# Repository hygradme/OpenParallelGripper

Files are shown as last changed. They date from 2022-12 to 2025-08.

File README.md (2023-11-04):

# Electric Parallel Gripper for UFACTORY LITE 6

## Introduction
This project provides electric parallel gripper for UFACTORY LITE 6.
This gripper can also be used for UFACTORY xArm series and possibly with other industrial cobots like Universal Robot etc.

Video (pick and place example with UFACTORY LITE 6 and OPEN Parallel Gripper): https://www.youtube.com/shorts/wrYzYbHsh44

There are two version available. SCS3045M_version which is original version I made and XL330_version which I redesigned to make the gripper lighter, thinner and cheaper at the expense of rigidity.
## SCS3045M_version
Detail: [SCS3045M_version](./SCS3045M_version/README.md)

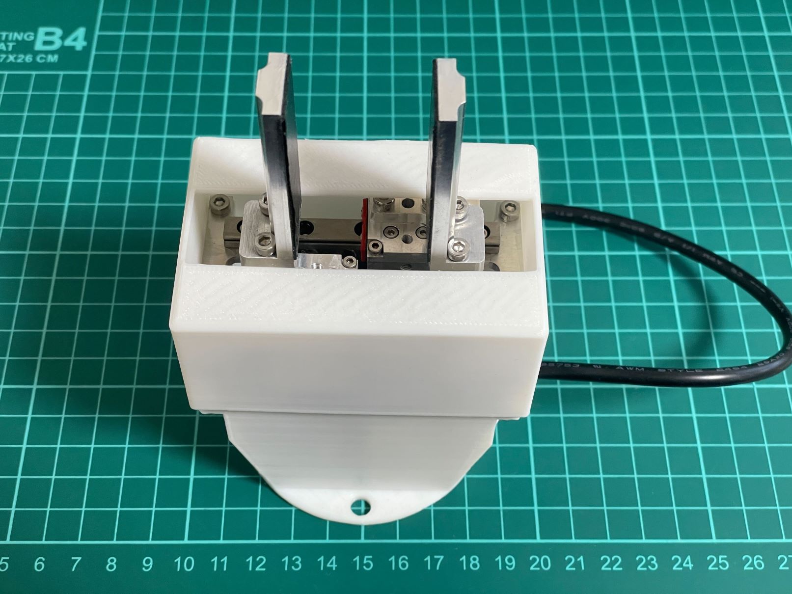
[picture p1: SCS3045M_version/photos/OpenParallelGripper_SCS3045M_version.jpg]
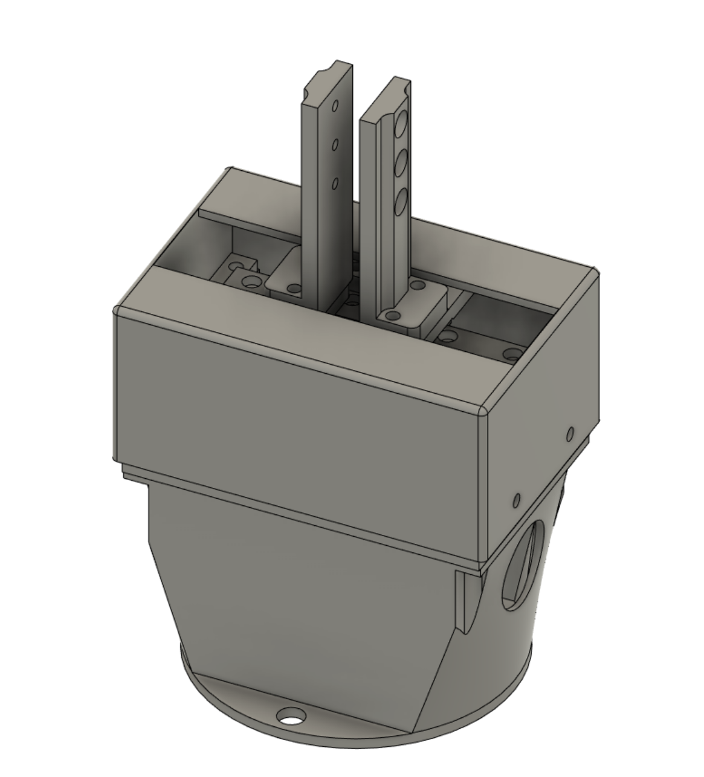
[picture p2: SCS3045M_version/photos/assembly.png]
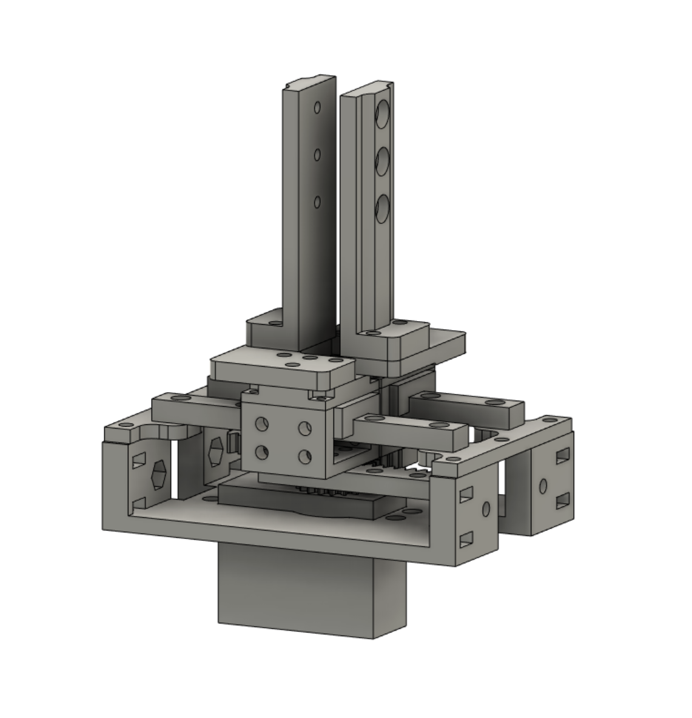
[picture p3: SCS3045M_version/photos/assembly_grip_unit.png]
  
- Use Feetech SCS3045M servo
- stroke: 0-55mm
- weight: about 340g
- Communication protocol: Two digital inputs(compatible with default LITE 6 gripper) or Modbus-RTU with RS485.

## XL330_version
Detail: [XL330_version](./XL330_version/README.md)

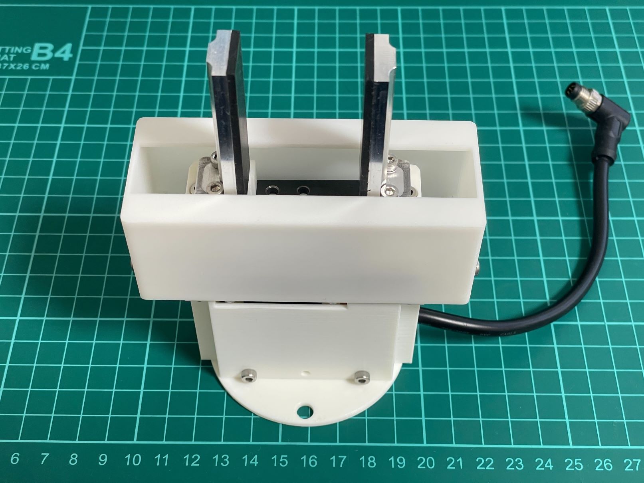
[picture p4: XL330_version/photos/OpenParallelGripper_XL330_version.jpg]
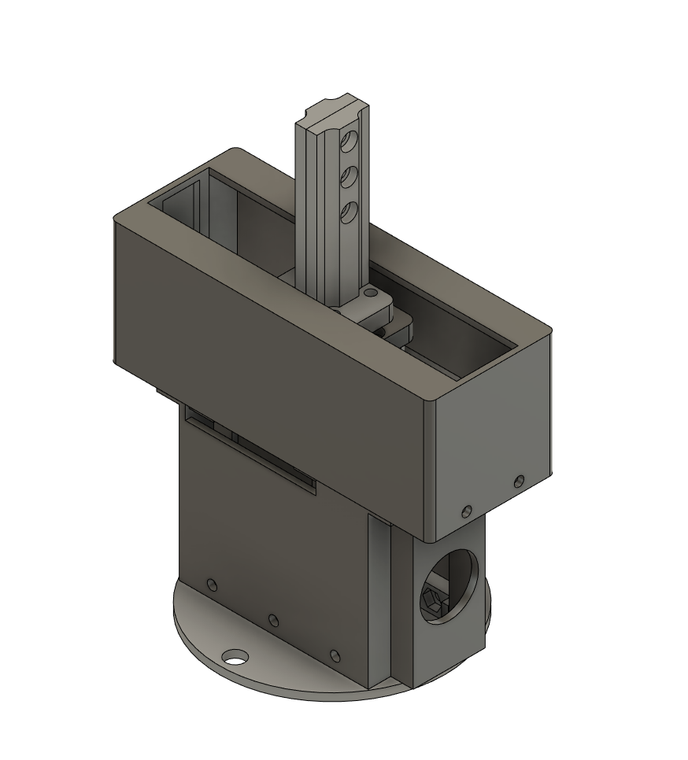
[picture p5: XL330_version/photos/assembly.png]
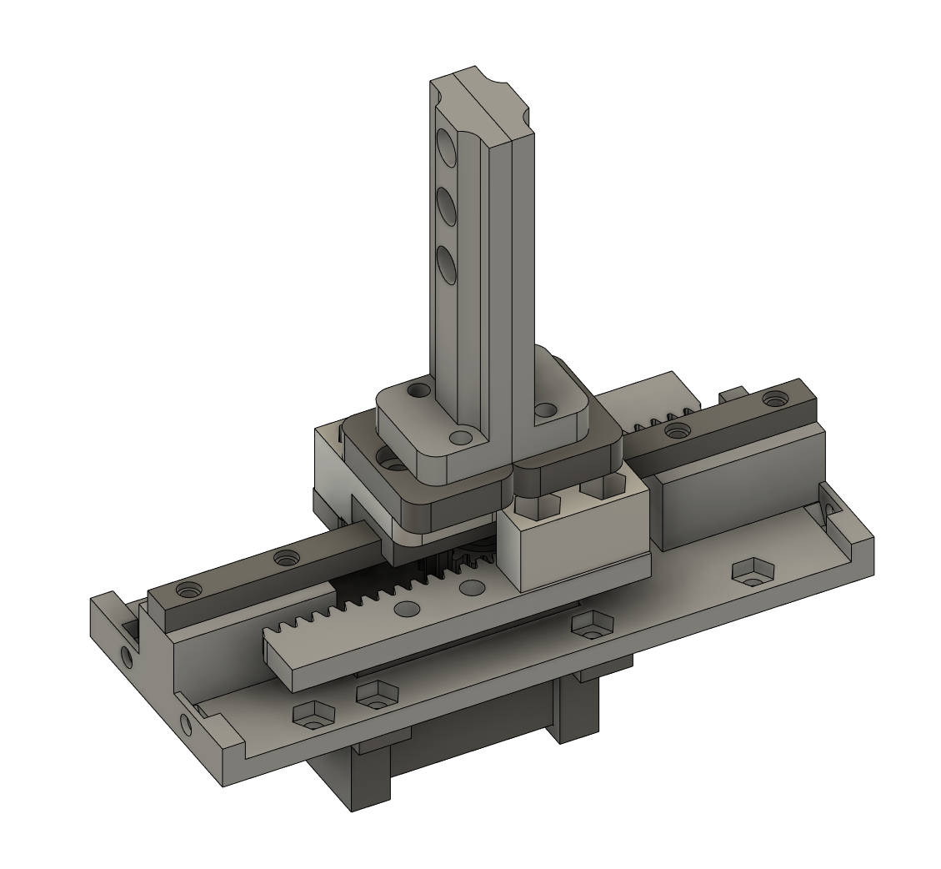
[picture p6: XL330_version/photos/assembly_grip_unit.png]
  
- Use Dynamixel XL330-M288-T servo
- stroke: 0-65mm
- weight: about 270g
- Communication protocol: Two digital inputs(compatible with default LITE 6 gripper) or Modbus-RTU with RS485.

## Contact
https://twitter.com/EL2031watson

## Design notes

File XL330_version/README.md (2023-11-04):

# Electric Parallel Gripper for UFACTORY LITE 6(XL330 version)

## Introduction
This project provides electric parallel gripper for UFACTORY LITE 6.
This gripper can also be used for UFACTORY xArm series and possibly with other industrial cobots like Universal Robot etc.

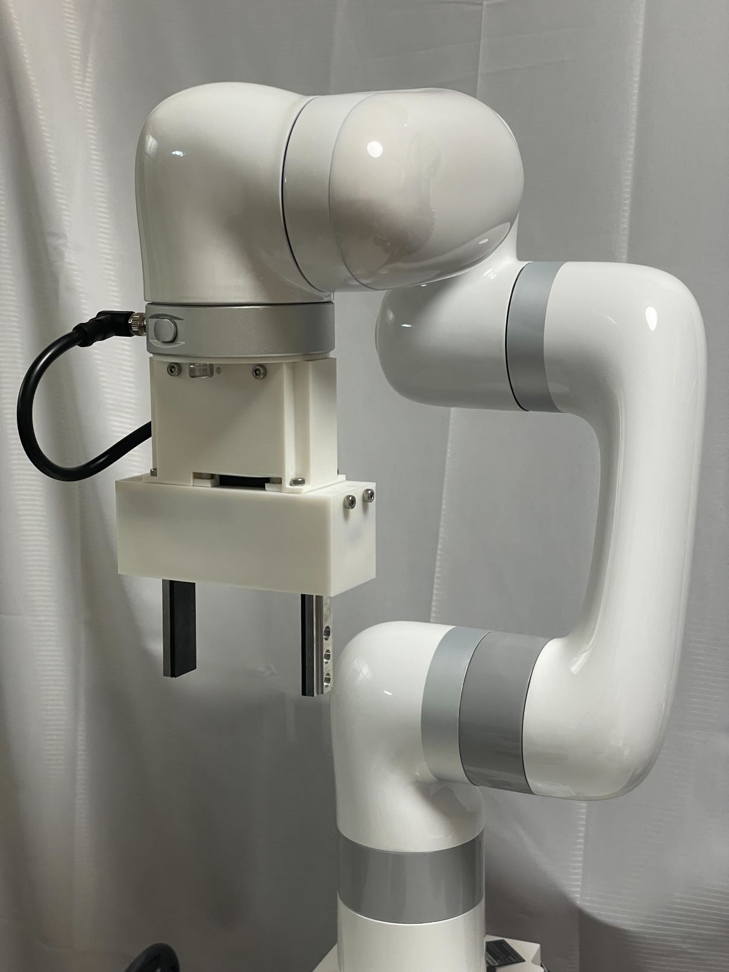
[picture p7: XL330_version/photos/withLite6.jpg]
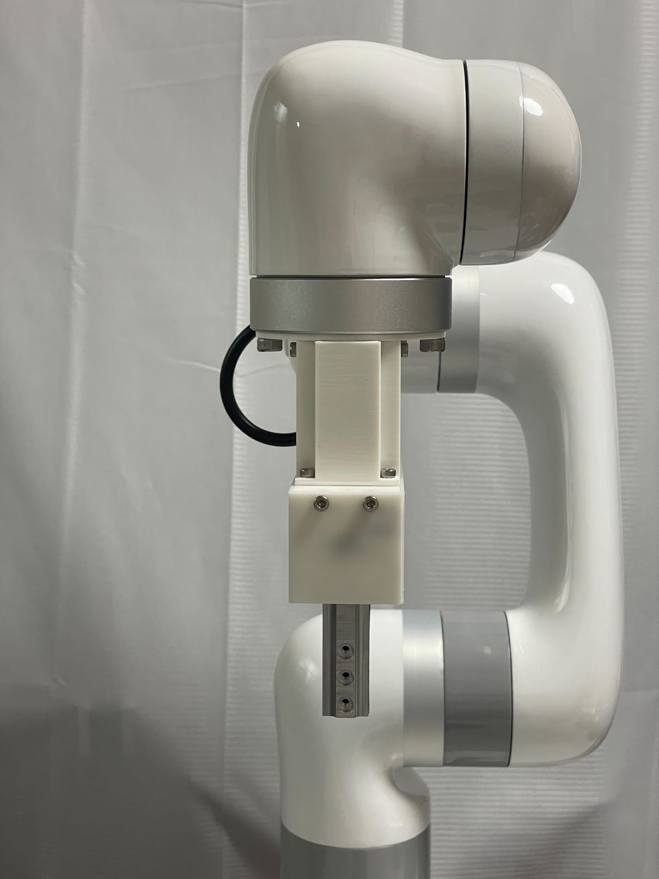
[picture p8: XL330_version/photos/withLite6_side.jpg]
 



 

Video (pick and place example with UFACTORY LITE 6 and OPEN Parallel Gripper): https://youtube.com/shorts/0Ie3bUuqNkI?si=m0Drl9e4QJItGcFO

## Spec of the gripper
- stroke: 0-65mm
- weight: about 270g
- Communication protocol: Two digital inputs(compatible with default LITE 6 gripper) or Modbus-RTU with RS485.

## BOM
Check [BOM](./hardware/BOM.md)

## Assemble instruction
Not yet avaialble.

## Electronics
See [Electronics](./electronics/README.md)
## Software
See [Software](./software/README.md)

If you prefer to use two digital inputs to control the gripper for simplicity, you can use xArm SDK from UFACTORY(https://github.com/xArm-Developer/xArm-Python-SDK/blob/master/xarm/wrapper/xarm_api.py#L3654).

If you want to control the gripper more detail, you need to use Modbus-RTU with RS485.

## Contact
https://twitter.com/EL2031watson

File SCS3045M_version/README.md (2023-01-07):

# Electric Parallel Gripper for UFACTORY LITE 6

## Introduction
This project provides electric parallel gripper for UFACTORY LITE 6.
This gripper can also be used for UFACTORY xArm series and possibly with other industrial cobots like Universal Robot etc.

 
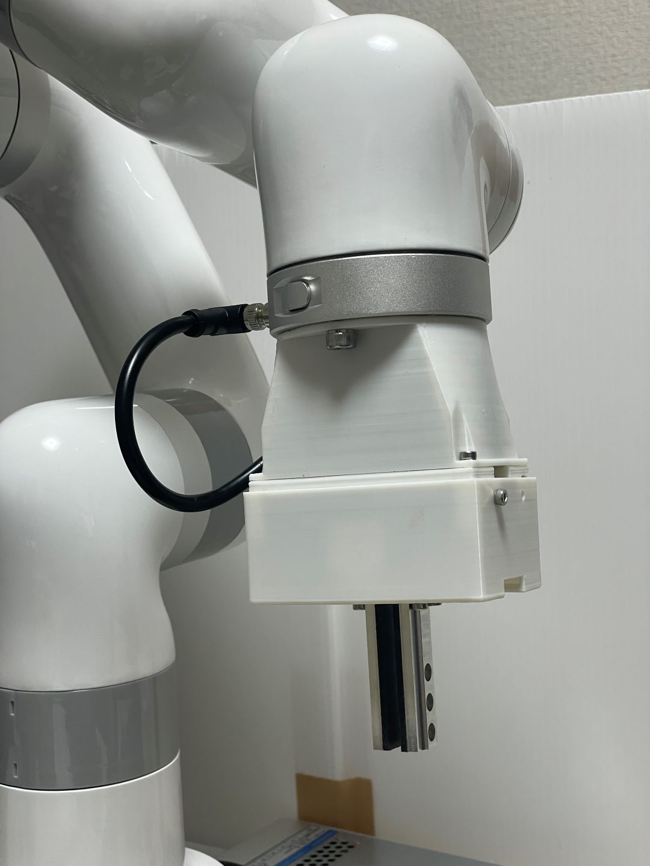
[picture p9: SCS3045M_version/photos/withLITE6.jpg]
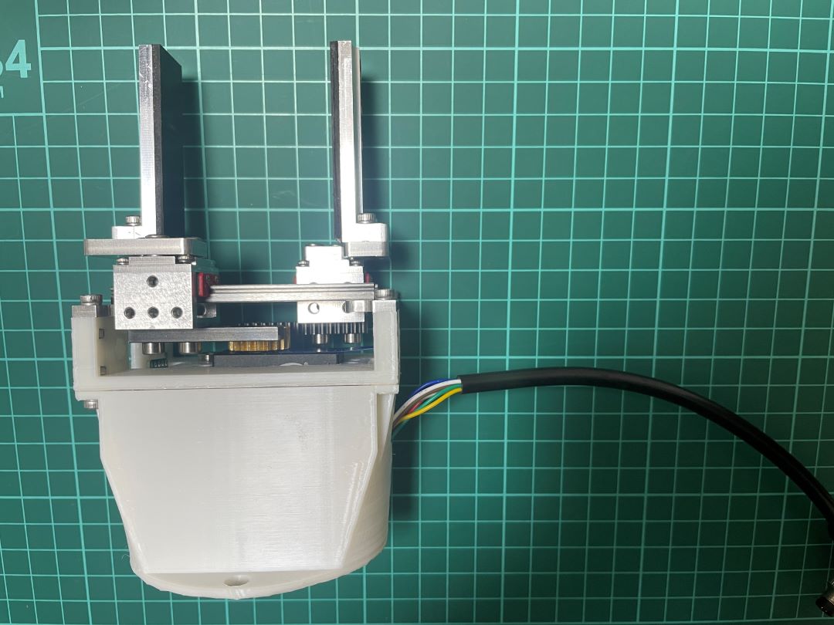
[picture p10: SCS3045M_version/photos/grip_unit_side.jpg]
 

Video (pick and place example with UFACTORY LITE 6 and OPEN Parallel Gripper): https://www.youtube.com/shorts/wrYzYbHsh44

## Spec of the gripper
- stroke: 0-55mm
- weight: about 340g
- Communication protocol: Two digital inputs(compatible with default LITE 6 gripper) or Modbus-RTU with RS485.

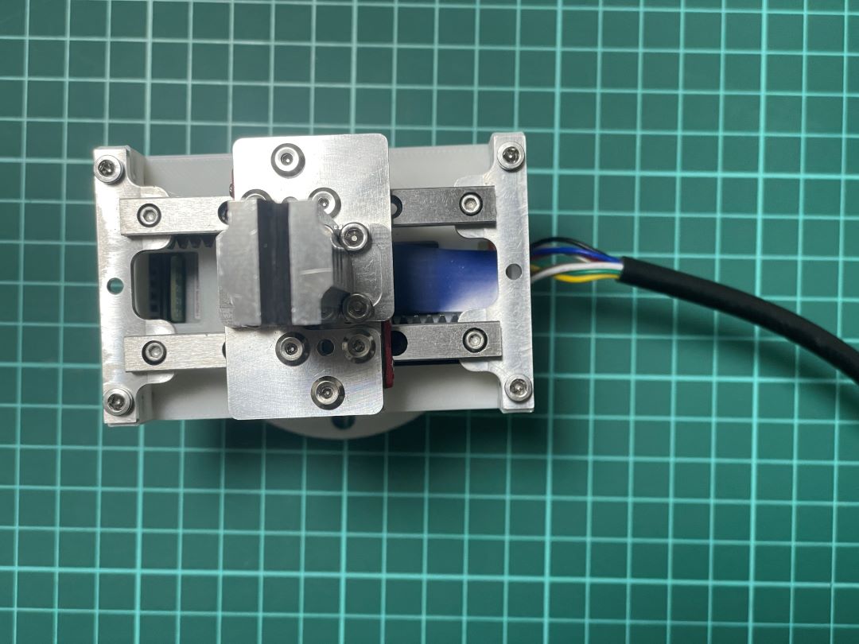
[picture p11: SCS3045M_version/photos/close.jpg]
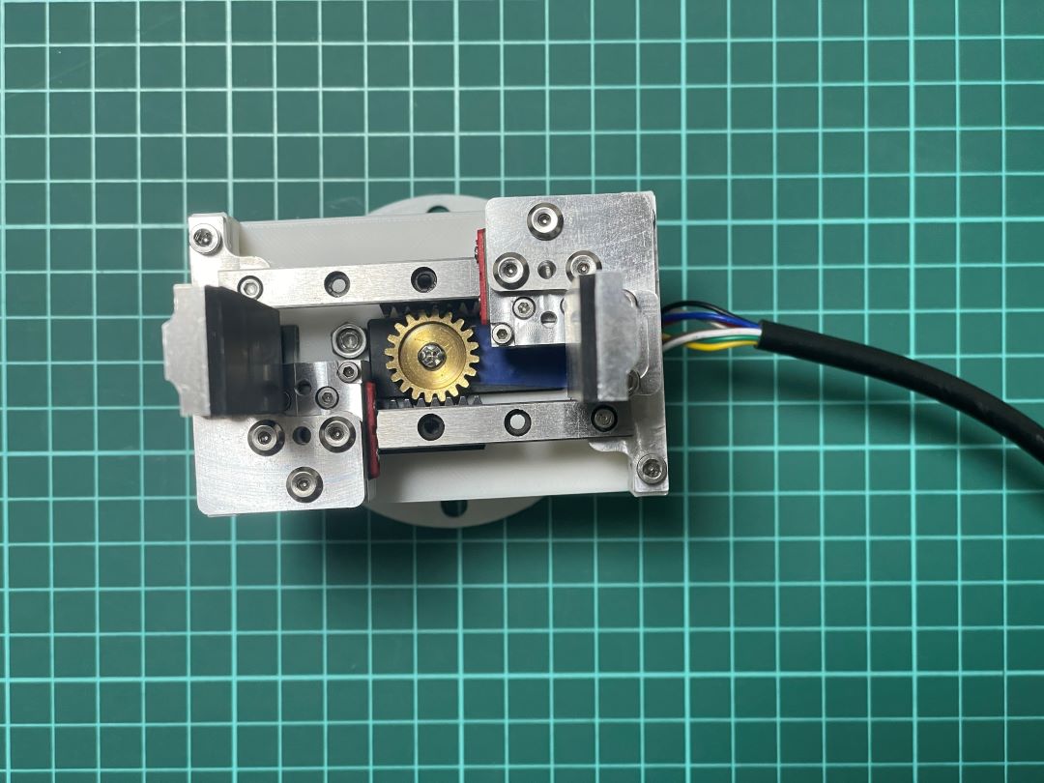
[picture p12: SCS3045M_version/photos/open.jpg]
 
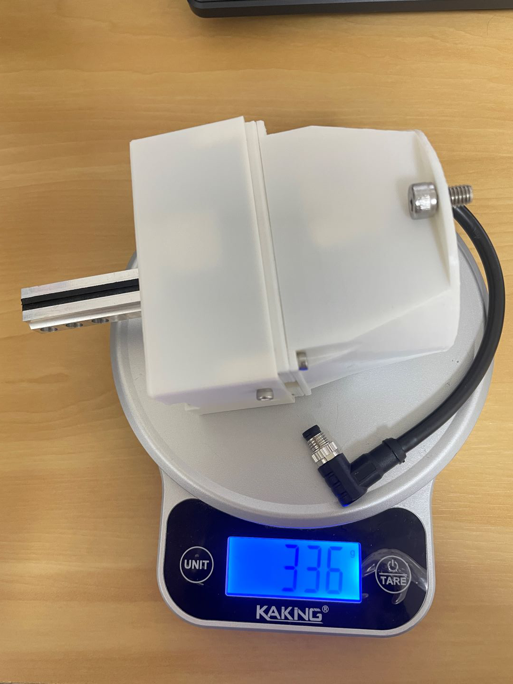
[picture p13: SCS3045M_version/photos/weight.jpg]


## BOM
Check [BOM](./hardware/BOM.md)

## Assemble instruction
Gripping module:

See https://www.youtube.com/watch?v=Q1Lmt6-BkuM

## Electronics
See [Electronics](./electronics/README.md)
## Software
See [Software](./software/README.md)

If you prefer to use two digital inputs to control the gripper for simplicity, you can use xArm SDK from UFACTORY(https://github.com/xArm-Developer/xArm-Python-SDK/blob/master/xarm/wrapper/xarm_api.py#L3654).

If you want to control the gripper more detail, you need to use Modbus-RTU with RS485.

## Contact
https://twitter.com/EL2031watson

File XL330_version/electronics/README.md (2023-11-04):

# OpenParalleGripper Electronics(XL330_version)

## Summary
Electronics are under development. The connection might be unstable. Soldering is required.

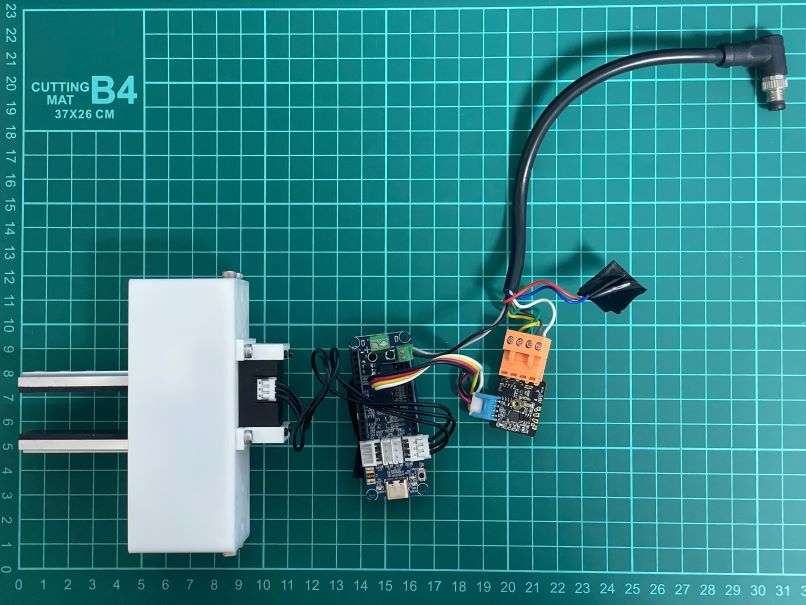
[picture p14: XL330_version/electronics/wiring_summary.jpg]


Need to make cross Grove cable to use Grove pin header since the alignment of TX and RX of OpenRB-150 is different from RS485 (switch white and yellow wires of Grove cable)

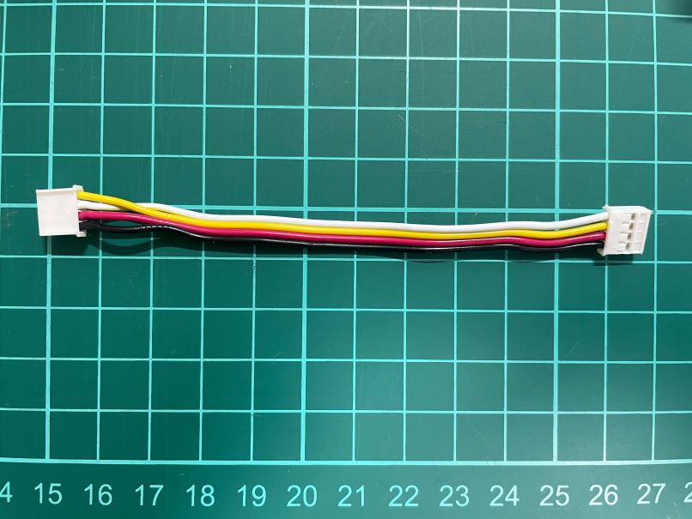
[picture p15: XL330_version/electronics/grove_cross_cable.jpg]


Need to add grove pin header and 2.54mm pitch terminal block
- Solder grove 4-pin header onto OpenRB-150 J12
- (Optinal) Put 2.54mm pitch terminal block onto PB10 and PB11 of OpenRB-150
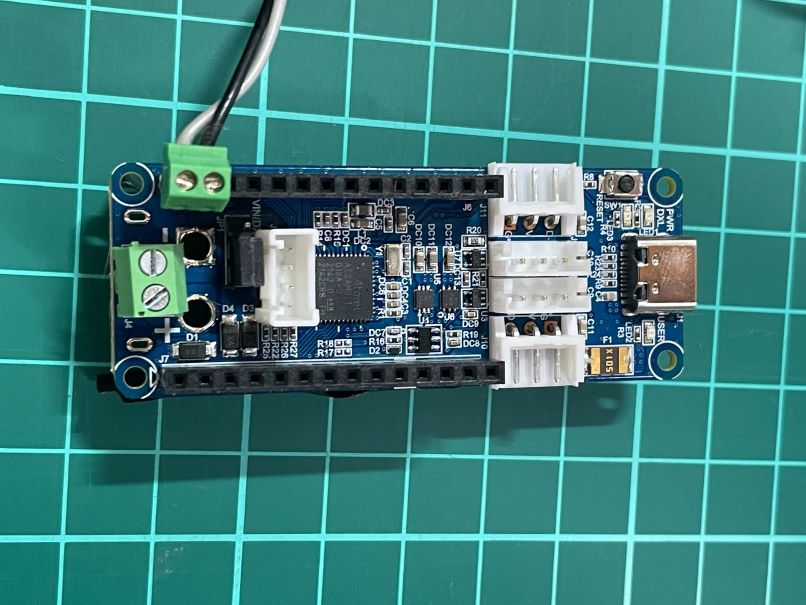
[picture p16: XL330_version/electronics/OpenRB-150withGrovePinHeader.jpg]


## Wiring
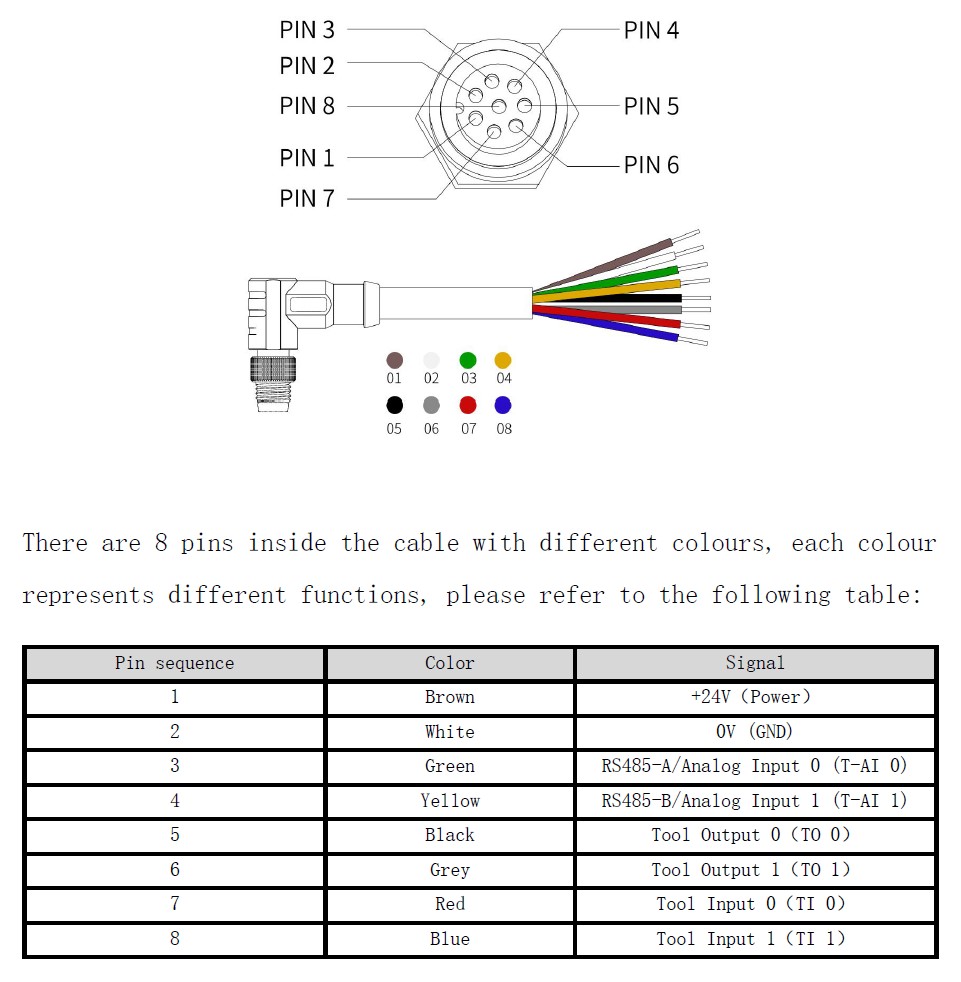
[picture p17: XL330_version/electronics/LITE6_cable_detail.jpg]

(https://www.ufactory.cc/_files/ugd/896670_f65d7d89fab64945b885876178bbafa7.pdf)

Connect cable, RS485 module, ATOM Lite, Debug board and servo motor as follow:
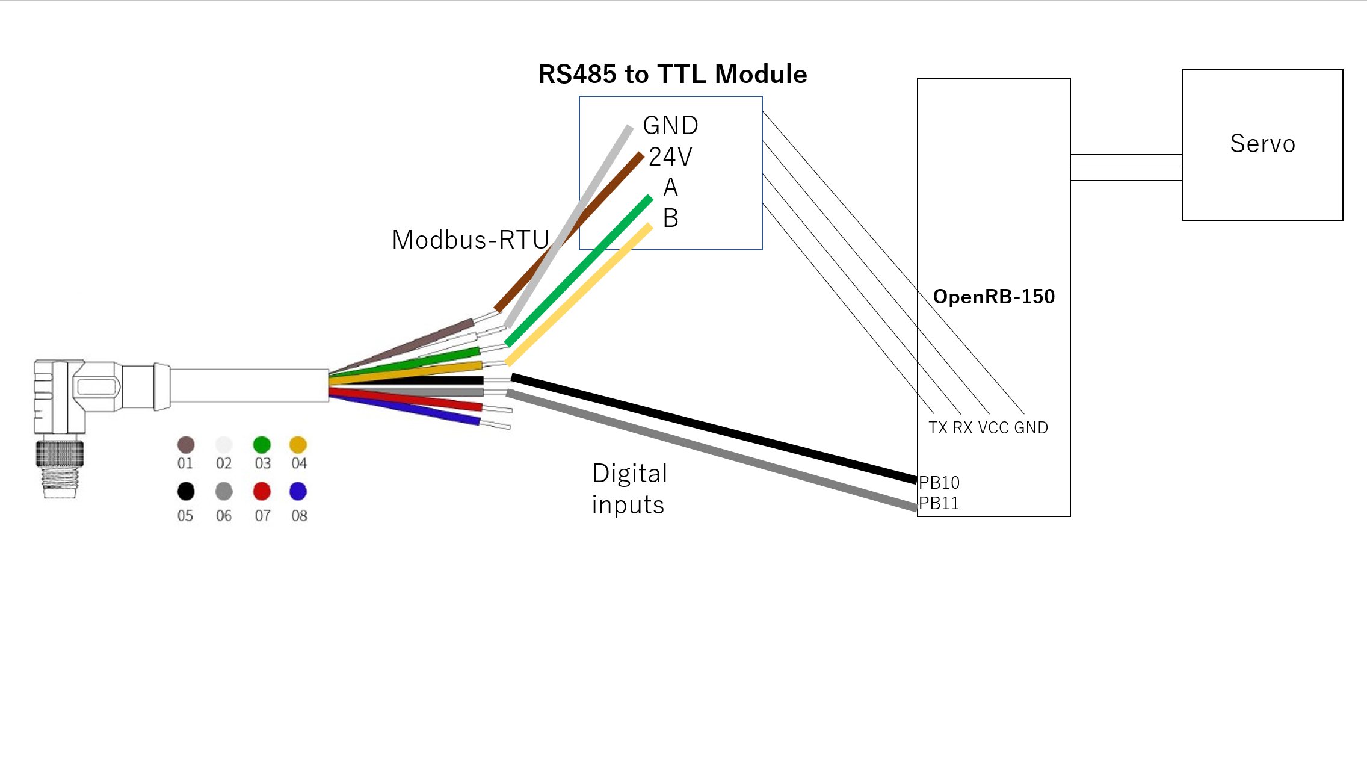
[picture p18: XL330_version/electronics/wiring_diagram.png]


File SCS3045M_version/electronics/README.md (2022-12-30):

# OpenParalleGripper Electronics

## Summary
Electronics are under development. The connection might be unstable. Soldering may need.

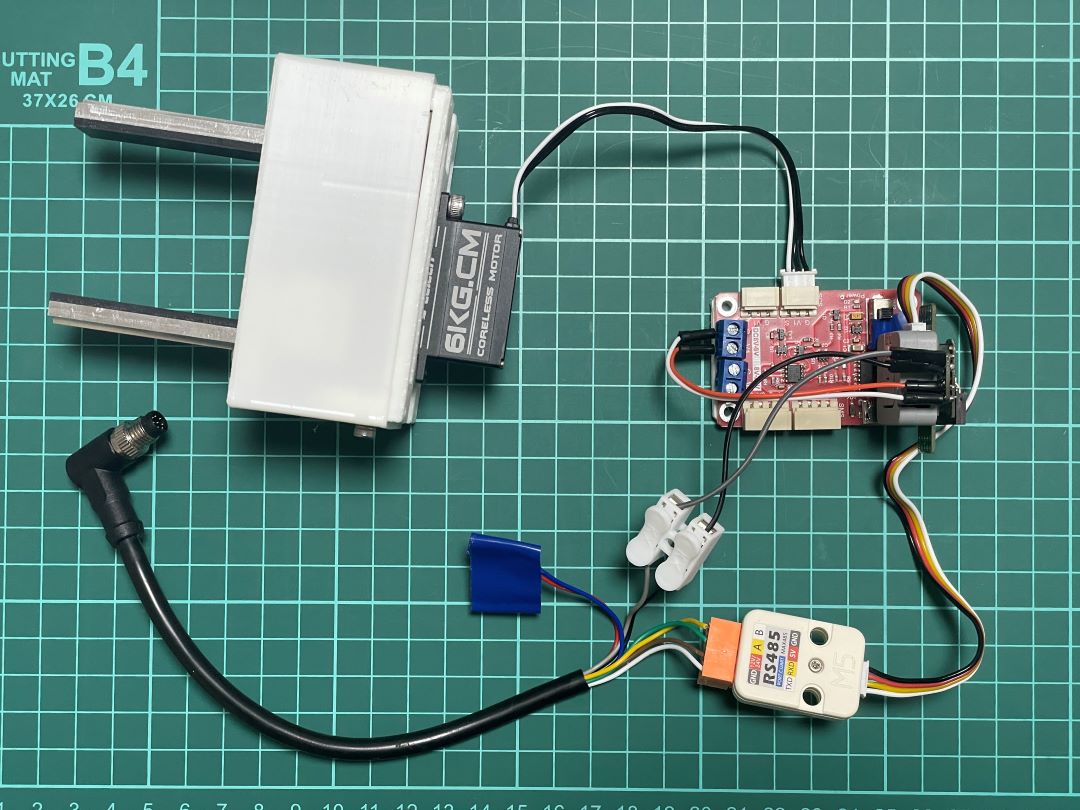
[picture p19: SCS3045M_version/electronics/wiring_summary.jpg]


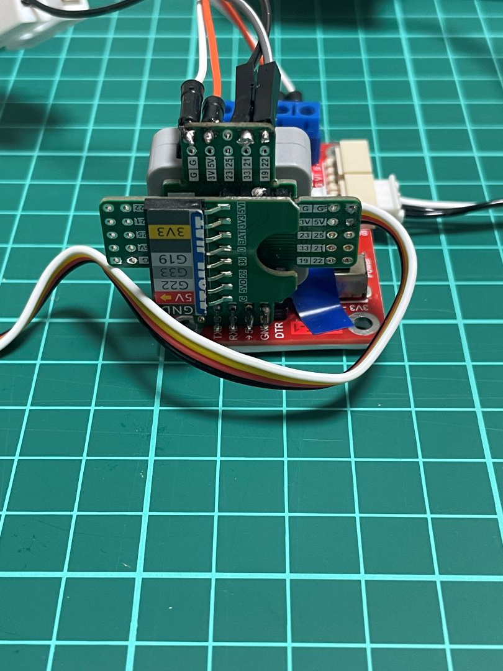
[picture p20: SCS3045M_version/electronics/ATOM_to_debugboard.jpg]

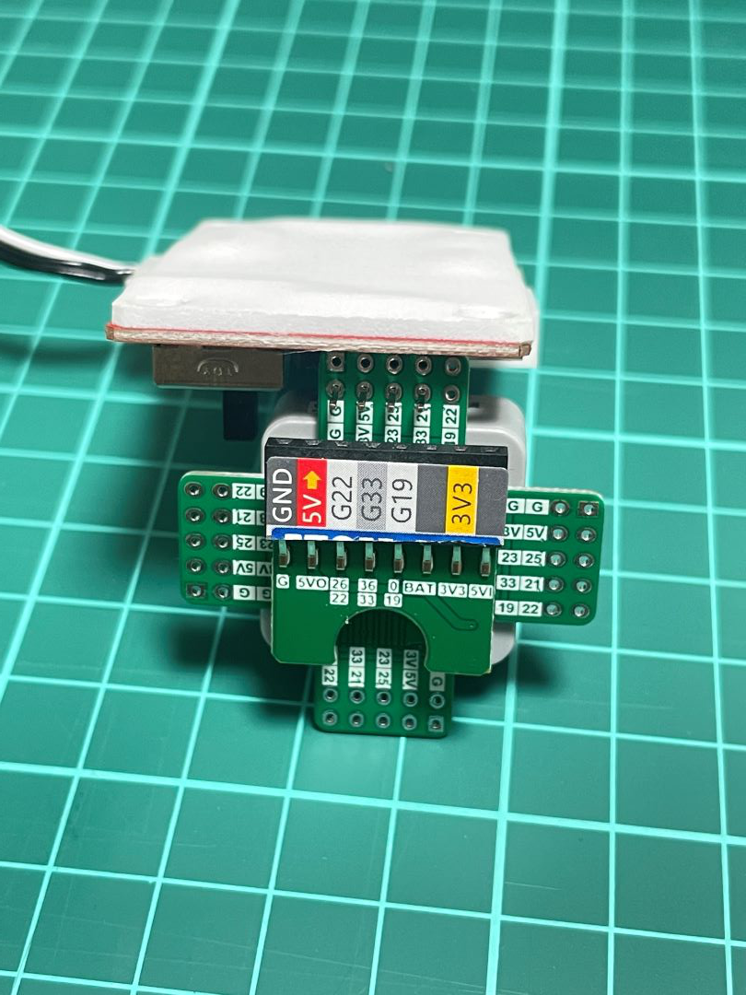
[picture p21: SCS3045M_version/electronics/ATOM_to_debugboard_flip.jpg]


## Wiring

(https://www.ufactory.cc/_files/ugd/896670_f65d7d89fab64945b885876178bbafa7.pdf)

Connect cable, RS485 module, ATOM Lite, Debug board and servo motor as follow:
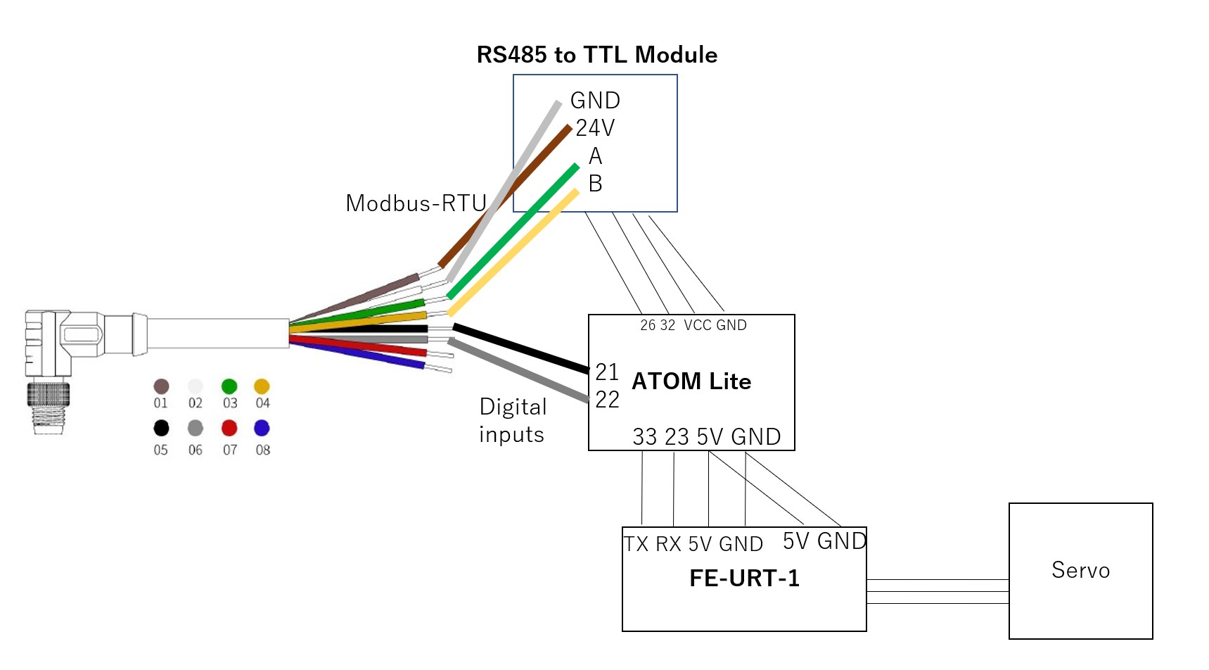
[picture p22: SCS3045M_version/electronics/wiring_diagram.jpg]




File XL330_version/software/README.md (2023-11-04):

# OpenParallelGripper Software
## Software part is under development so you may need some effort to work this gripper.

## Summary
To control the gripper, you need to use either digital inputs from tool IO of LITE 6 or Modbus-RTU through RS485 of tool IO of LITE 6.

## Requirement

### Arduino IDE

- Modbus-RTU Library (https://github.com/emelianov/modbus-esp8266)
- DYNAMIXEL2Arduino (https://github.com/ROBOTIS-GIT/dynamixel2arduino)

### PythonSDK
- xArm-Python-SDK(https://github.com/xArm-Developer/xArm-Python-SDK)

## Installation
Connect your OpenRB-150 to your PC and write the sketch software/arduino_sketch/OpenRB_modbusRTU.ino into your OpenRB-150.

Then run either of python script to open and close your gripper.

```
# For Modbus-RTU control
$ python3 control_openRB150_with_modbus_rtu.py <IP address of arm> oc

# For digital input control
$ python3 control_openRB150_with_lite6_api.py <IP address of arm> oc
```

The 2nd argument is list of action. "o" means open and "c" means close.
```
# Just open the gripper
$ python3 control_openRB150_with_lite6_api.py <IP address of arm> o

# Just close the gripper
$ python3 control_openRB150_with_lite6_api.py <IP address of arm> c

# Open and Close the gripper 4th times
$ python3 control_openRB150_with_lite6_api.py <IP address of arm> ococococ
```

Using Modbus-RTU interface, you can move the gripper stroke to the state between Open-Close.
```
import sys

from control_openRB150_with_modbus_rtu import ParalleGripperOpenRB150

ip = sys.argv[1]
arm = XArmAPI(ip, is_radian=False)
pga = ParalleGripperOpenRB150(arm)
storke = 100 # deg in servo axis. range is 0-250 for 65mm stroke gripper.
pga.move(stroke)
storke = 50
pga.move(stroke)

```

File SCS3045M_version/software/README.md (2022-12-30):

# OpenParallelGripper Software
## Software part is under development so you may need some effort to work this gripper.

## Summary
To control the gripper, you need to use either digital inputs from tool IO of LITE 6 or Modbus-RTU through RS485 of tool IO of LITE 6.

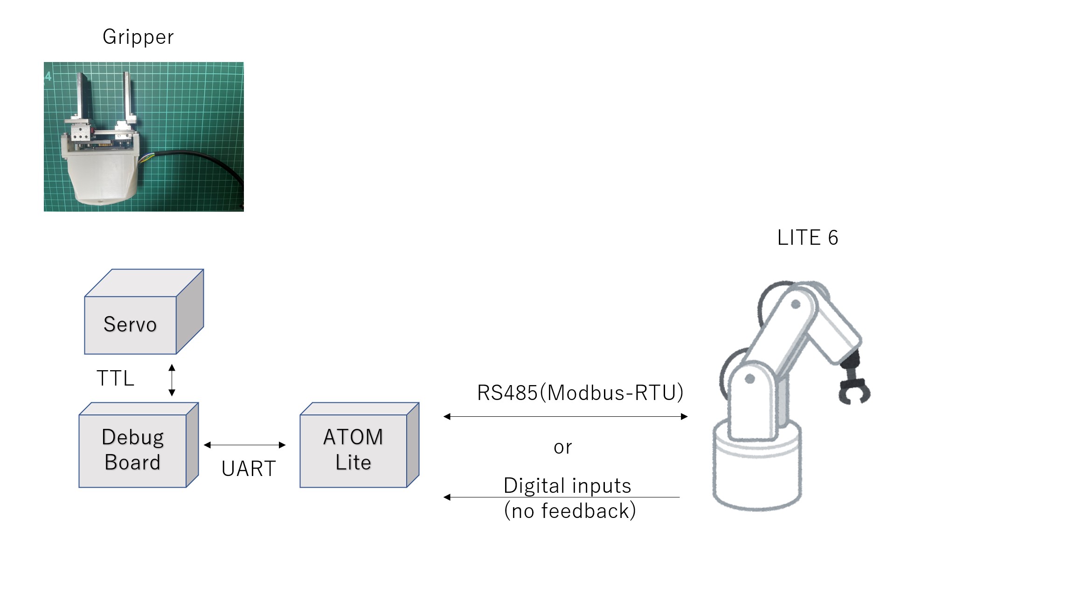
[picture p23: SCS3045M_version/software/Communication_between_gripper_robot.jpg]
Gripper-Arm communication


## Requirement

### Arduino IDE
- Feetech Servo Library (https://akizukidenshi.com/download/ds/feetech/SCServo.zip)
- Modbus-RTU Library (https://github.com/emelianov/modbus-esp8266)
- M5Atom Library (https://github.com/m5stack/M5Atom)

### PythonSDK
- xArm-Python-SDK(https://github.com/xArm-Developer/xArm-Python-SDK)

## Installation
Connect your ATOM Lite to PC and write the sketch software/gripper_driver/ModbusRTU_SCSServo.ino into your ATOM Lite.

Then run either of python script to open and close your gripper.

```
# for Modbus-RTU control
$ python3 control_with_modbus_rtu.py <IP address of arm> oc

# for digital input control
$ python3 control_with_lite6_api.py <IP address of arm> oc
```

The 2nd argument is list of action. "o" means open and "c" means close.
```
# Just open the gripper
$ python3 control_with_lite6_api.py <IP address of arm> o

# Just close the gripper
$ python3 control_with_lite6_api.py <IP address of arm> c

# open and close the gripper 4th times
$ python3 control_with_lite6_api.py <IP address of arm> ococococ
```

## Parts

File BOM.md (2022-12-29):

# Electric Parallel Gripper Bill Of Materials

## 1. 3D print parts (stl files are available in parts/3dprint_parts/stl)
  - Base x1
  - TipCover x1
  - ToArm x1

## 2. CNC Miling parts
  - claw_base x2
  - claw50mm x2
  - rail_base_holder x2
  - rail_fixer x2
  - rack_to_rail_base x2

## 3. parts from shops
  - SCS3045M x1 (https://www.aliexpress.com/item/1005002219505397.html)
  - gear_20tooth x1 (https://www.servocity.com/32p-20-tooth-25t-3f-spline-servo-mount-gears/)
  - SSEB8-70 x2 (https://jp.misumi-ec.com/vona2/detail/110302586530/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)
  (This may fits too https://www.amazon.com/dp/B01L88R8SY)
  - RGEAL0.8KA-40-A5-B10-C10-D10 x2 (https://jp.misumi-ec.com/vona2/detail/110300429920/?ProductCode=RGEAL0.8KA-40-A5-B10-C10-D10)
  - M2x4mm bolt x 8
  - M2x6mm bolt x 8
  - M2.3x5mm bolt x4
  - M3x8mm bolt x22
  - M3.5x6mm bolt x4
  - M4x6mm bolt x 4
  - M6x10mm bolt x2
  - M3 nut x12
  - M4 nut x4

## 4. electronic components (Just for reference. You can choose your own micro controller and other components to control the servo motor)
  - FE-URT1-C001 (https://www.aliexpress.com/item/1005001803208568.html)
  - ATOM Lite(https://shop.m5stack.com/products/atom-lite-esp32-development-kit)
  - RS485 to TTL Converter Unit (https://shop.m5stack.com/products/rs485-module)
  - ATOM Mate Adapter DIY Expansion Kit (https://shop.m5stack.com/products/atom-mate)
  -  Lite 6 end adapter cable (Ask UFactory to purchase)
  - Wires

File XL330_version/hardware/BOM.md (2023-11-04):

# Electric Parallel Gripper Bill Of Materials(XL330 version)

## 1. 3D print parts
stl files are available in ./3dprint_parts/stl
  - [Base](./3dprint_parts/stl/XL330_base_for65mm.stl) x1
  - [TipCover](./3dprint_parts/stl/TipCover_for65mm.stl) x1
  - [ToArm](./3dprint_parts/stl/ToArm.stl) x1
  - [R75_cover](./3dprint_parts/stl/R75_cover.stl) x1
  - [XL330_cover](./3dprint_parts/stl/XL330_cover.stl) x2
  - [Rail_base_to_rack](./3dprint_parts/stl/Rail_base_to_rack_dynamixel.stl) x2
  - [Claw_adapter](./3dprint_parts/stl/claw_adapter.stl) x2

Note: To keep the gripper weight small, thickness of these parts are thin.

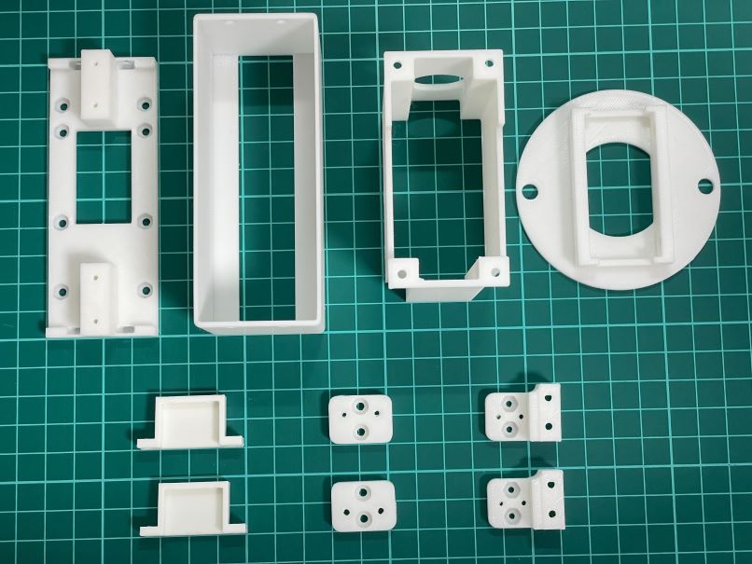
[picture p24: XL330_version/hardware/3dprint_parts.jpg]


  - [Gear20Tooth_forXL330](./3dprint_parts/stl/Gear20Tooth_forXL330.stl) x1 (3D printing with metal material strongly reccomended. I used SLM)

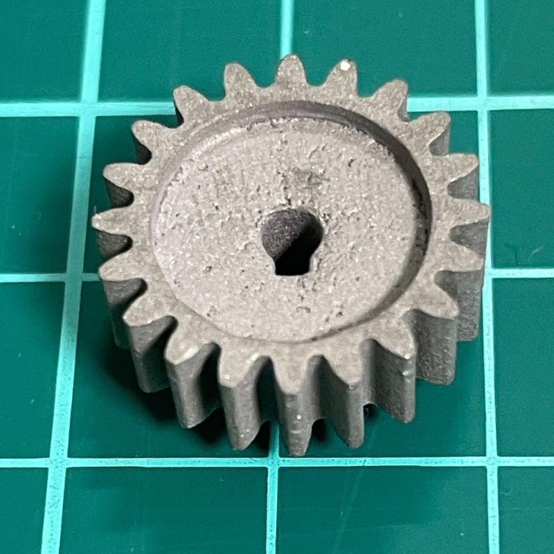
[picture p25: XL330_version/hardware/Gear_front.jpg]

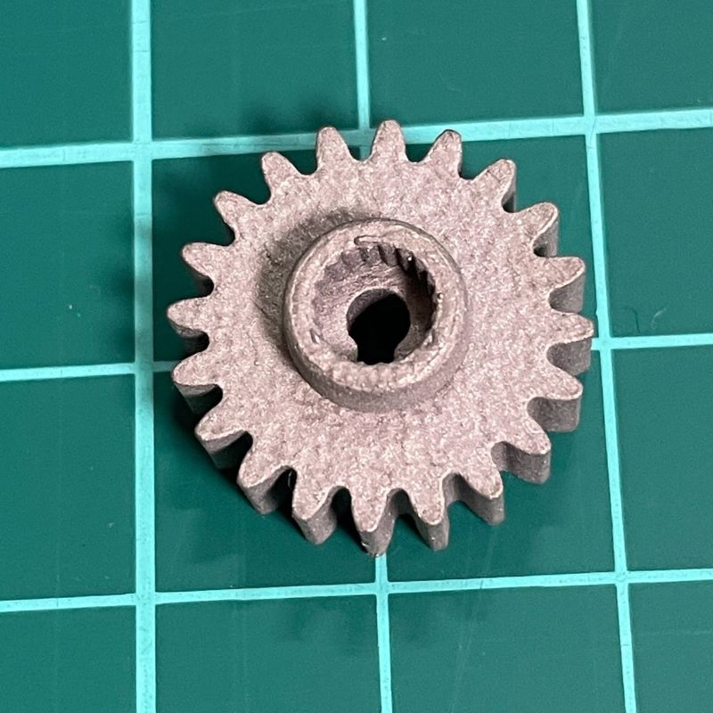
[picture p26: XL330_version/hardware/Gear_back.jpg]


## 2. CNC Miling parts
step files and drawings are available in ./cnc_miling_parts/
Optionally, stl files for 3d printing are also available but these parts need stiffness so I recommend to use Aluminum for these parts.

  - [Claw50mm](./cnc_miling_parts/Claw_50mm.step) x2

## 3. parts from shops
  - XL330-M288-T x1 (https://emanual.robotis.com/docs/en/dxl/x/xl330-m288/)
  - SSE2B6-100 x1 (https://us.misumi-ec.com/vona2/detail/110302586530/?HissuCode=SSE2B6-100)
  - RGEAL0.8KA-55-A5-B10-C10-D10 x2 (https://us.misumi-ec.com/vona2/detail/110300429920/?HissuCode=RGEAL0.8KA-55-A5-B10-C10-D10)

- M6 x 10mm x2
- M3.5 x 8mm x 4
- M3x8mm x 20
- M3x6mm x 4
- M2 x 4mm x 4
- M2 x 6mm x 4
- M2 Tapping screw x 4 (Included in Dynamixel XL330 package)
- M3.5 Nuts x 4
- M3 Nuts x 24
- M2 Nuts x 4

## 4. electronic components (Just for reference. You can choose your own micro controller and other components to control the servo motor)
  - OpenRB-150(https://emanual.robotis.com/docs/en/parts/controller/openrb-150/)

      (OpenRB-150 with XL330-M288-T set is alaso avaiable: https://www.robotis.us/openrb-150/)
  - RS485 to TTL Converter Unit (https://shop.m5stack.com/products/rs485-module)
  -  Lite 6 end adapter cable (Included in Lite 6. If not, ask UFACTORY to purchase)
  - Wires

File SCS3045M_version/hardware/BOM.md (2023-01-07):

# Electric Parallel Gripper Bill Of Materials

## 1. 3D print parts 
stl files are available in ./3dprint_parts/stl
  - [Base](./3dprint_parts/stl/SCS3045MBase.stl) x1
  - [TipCover](./3dprint_parts/stl/TipCover.stl) x1
  - [ToArm](./3dprint_parts/stl/ToArm.stl) x1

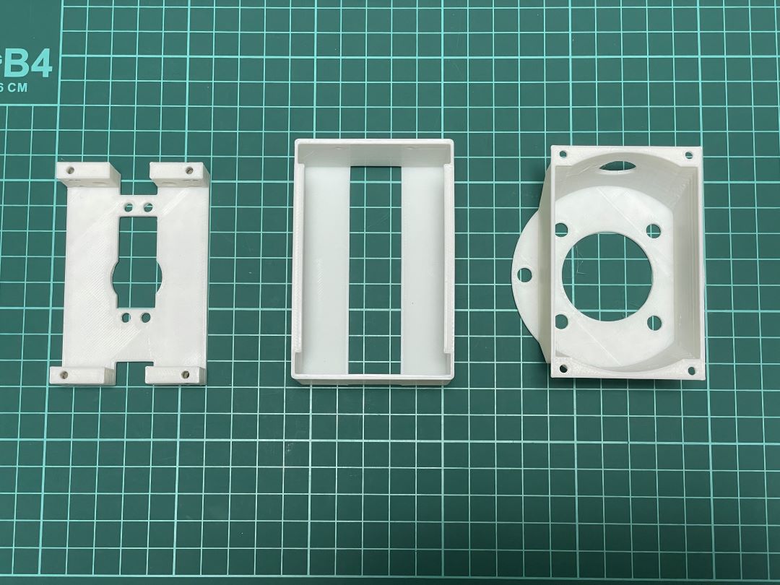
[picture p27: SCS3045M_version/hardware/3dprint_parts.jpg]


Note: To keep the gripper weight small, thickness of these parts are thin.

## 2. CNC Miling parts
step files and drawings are available in ./cnc_miling_parts/  
Optionally, stl files for 3d printing are also available but these parts need stiffness so I recommend to use Aluminum for these parts.
  - [claw_base](./cnc_miling_parts/claw_base.step) ([drawing](./cnc_miling_parts/drawing/claw_base.pdf)) x2
  - [claw50mm](./cnc_miling_parts/claw50mm.step) ([drawing](./cnc_miling_parts/drawing/claw50mm.pdf)) x2
  - [rail_base_holder](./cnc_miling_parts/rail_base_holder.step) ([drawing](./cnc_miling_parts/drawing/rail_base_holder.pdf)) x2
  - [rail_fixer](./cnc_miling_parts/rail_fixer.step) ([drawing](./cnc_miling_parts/drawing/rail_fixer_edit.pdf)) x2
  - [rack_to_rail_base](./cnc_miling_parts/rack_to_rail_base.step) ([drawing](./cnc_miling_parts/drawing/rack_to_rail_base.pdf)) x2

## 3. parts from shops
  - SCS3045M x1 (https://www.aliexpress.com/item/1005002219505397.html)
  - gear_20tooth x1 (https://www.servocity.com/32p-20-tooth-25t-3f-spline-servo-mount-gears/)
  - SSEB8-70 x2 (https://jp.misumi-ec.com/vona2/detail/110302586530/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)
  (This may fits too https://www.amazon.com/dp/B01L88R8SY)
  - RGEAL0.8KA-40-A5-B10-C10-D10 x2 (https://jp.misumi-ec.com/vona2/detail/110300429920/?ProductCode=RGEAL0.8KA-40-A5-B10-C10-D10)
  - M2x4mm bolt x 8
  - M2x6mm bolt x 8
  - M2.3x5mm bolt x4
  - M3x8mm bolt x22
  - M3.5x6mm bolt x4
  - M4x6mm bolt x 4
  - M6x10mm bolt x2
  - M3 nut x12
  - M4 nut x4

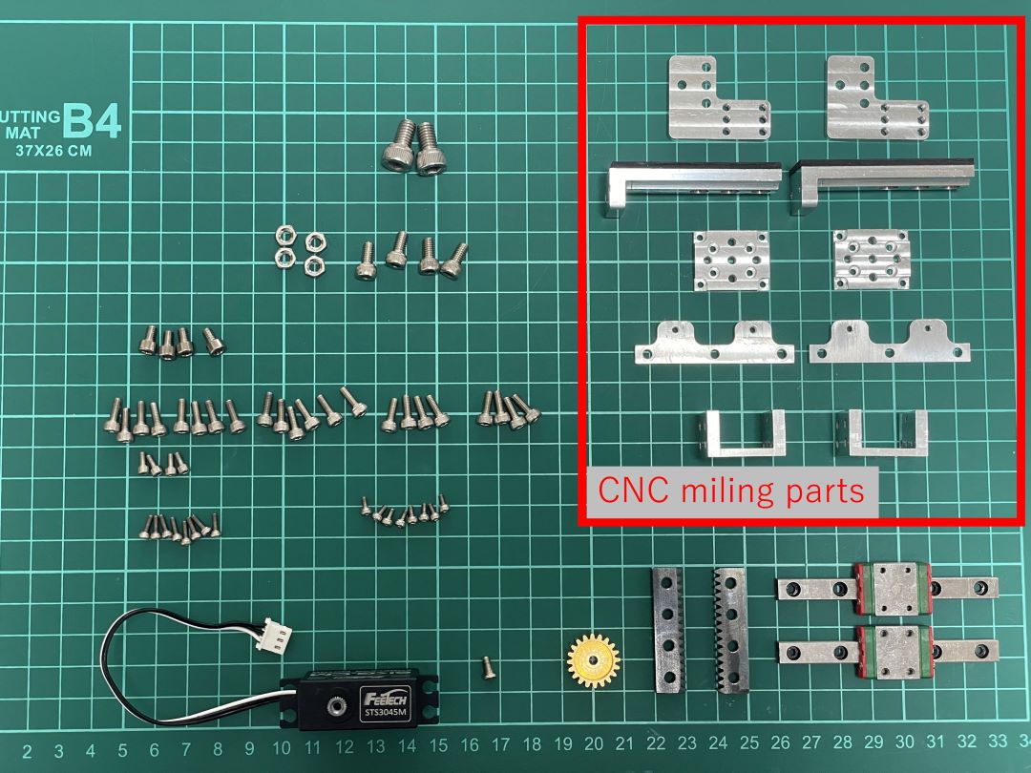
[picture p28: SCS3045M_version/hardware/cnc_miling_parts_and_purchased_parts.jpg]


## 4. electronic components (Just for reference. You can choose your own micro controller and other components to control the servo motor)
  - FE-URT1-C001 (https://www.aliexpress.com/item/1005001803208568.html)
  - ATOM Lite(https://shop.m5stack.com/products/atom-lite-esp32-development-kit)
  - RS485 to TTL Converter Unit (https://shop.m5stack.com/products/rs485-module)
  - ATOM Mate Adapter DIY Expansion Kit (https://shop.m5stack.com/products/atom-mate)
  -  Lite 6 end adapter cable (Ask UFactory to purchase)
  - Wires

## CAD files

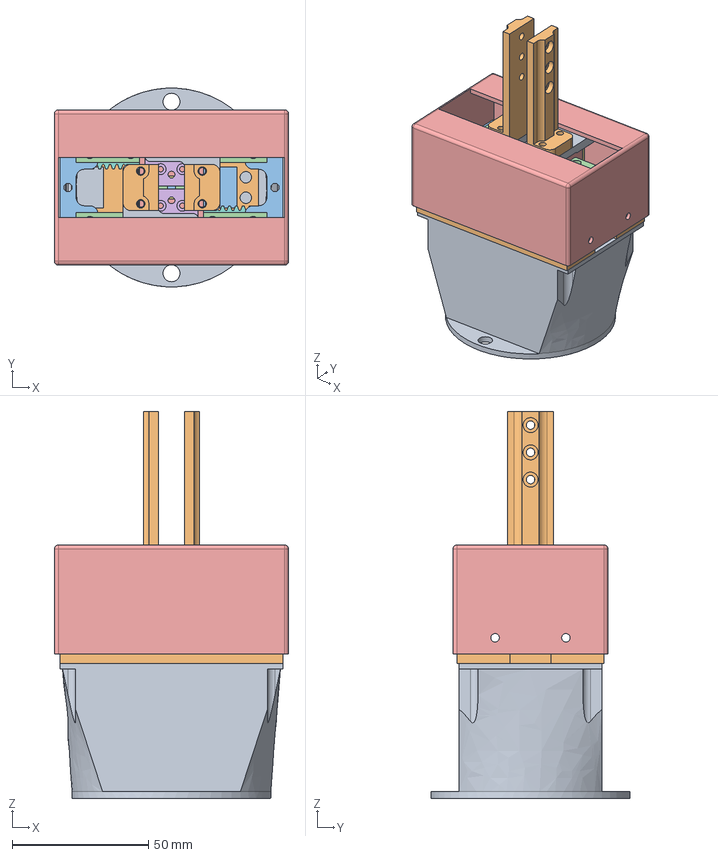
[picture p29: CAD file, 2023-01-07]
SCS3045M_version/hardware/gripper_assembly.step
86.0 x 73.0 x 142.1 mm
ToArm
SCS3045MBase
rail_fixer x 2
RSEB8-70_rail x 2
RSEB8-70_base x 2
rail_base_holder x 2
rack_to_rail_base x 2
Rack Gear (16 teeth) x 2
claw_base x 2
claw_50mm x 2
SCS3045M
gear_20tooth
TipCover

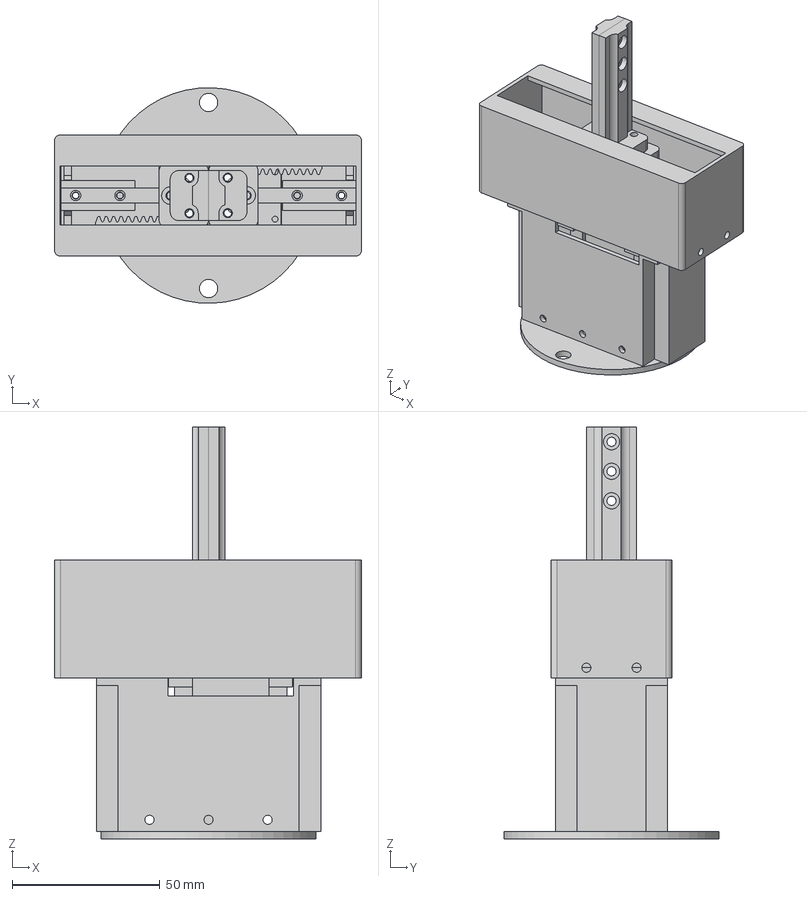
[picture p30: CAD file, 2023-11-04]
XL330_version/hardware/gripper_assembly.step
104.0 x 73.0 x 139.5 mm
R75_cover
ToArm
XL330_base_for65mm
XL330_cover x 2
ref_XL330
Dynamixel_Gear20Tooth_forXL330
ref_SSE2B6-100_rail_100mm
ref_SSE2B6-100_base x 2
rail_base_to_rack_dynamixel x 2
claw_adapter x 2
claw_50mm x 2
TipCover_for65mm
ref_RGEAL0.8KA-55-A5-B10-C10-D10 x 2

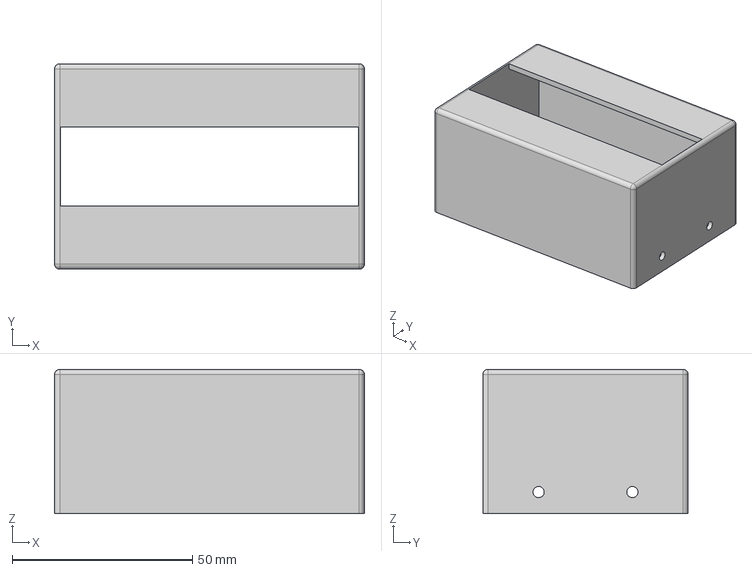
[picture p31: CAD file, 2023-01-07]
SCS3045M_version/hardware/3dprint_parts/TipCover.step
86.0 x 57.0 x 40.1 mm

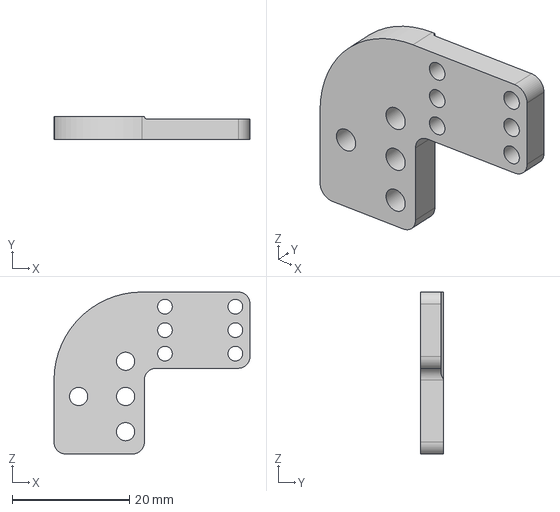
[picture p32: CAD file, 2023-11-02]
SCS3045M_version/hardware/cnc_miling_parts/claw_base_v2.step
33.4 x 4.00 x 27.6 mm

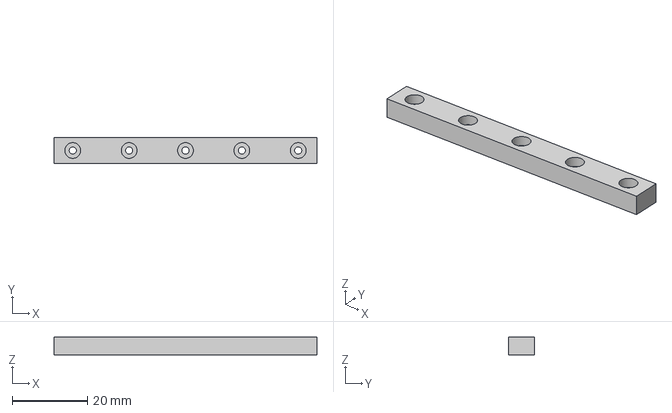
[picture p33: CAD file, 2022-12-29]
SCS3045M_version/hardware/purchase_parts/RSEB8-70_rail.step
70.0 x 7.00 x 4.70 mm

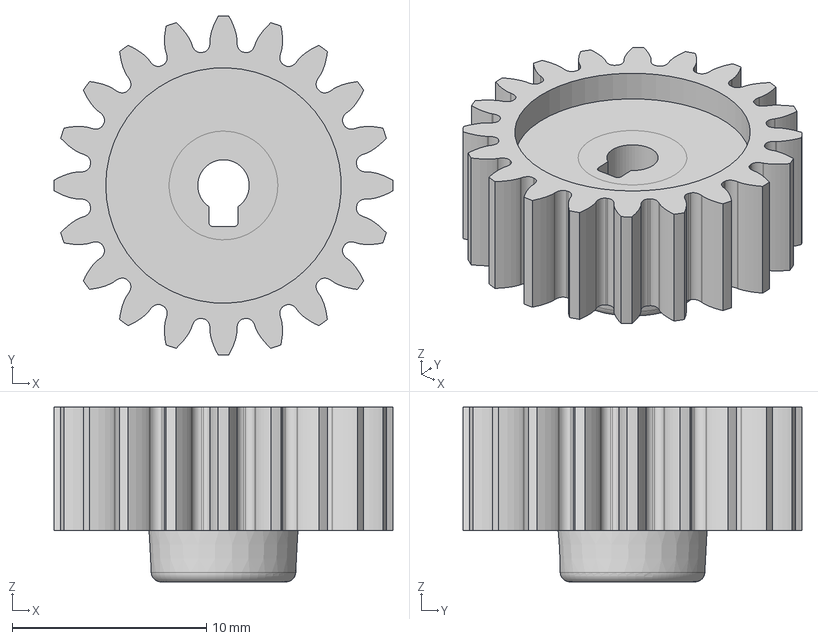
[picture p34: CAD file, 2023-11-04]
XL330_version/hardware/3dprint_parts/stp/Gear20Tooth_forXL330.step
17.5 x 17.5 x 9.00 mm

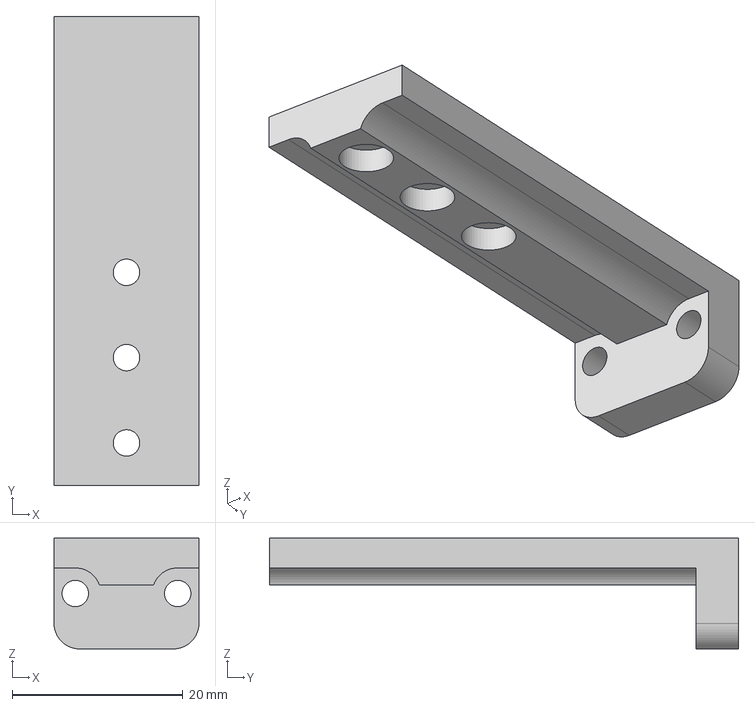
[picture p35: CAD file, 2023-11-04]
XL330_version/hardware/cnc_miling_parts/stp/Claw_50mm.step
17.0 x 55.0 x 13.0 mm

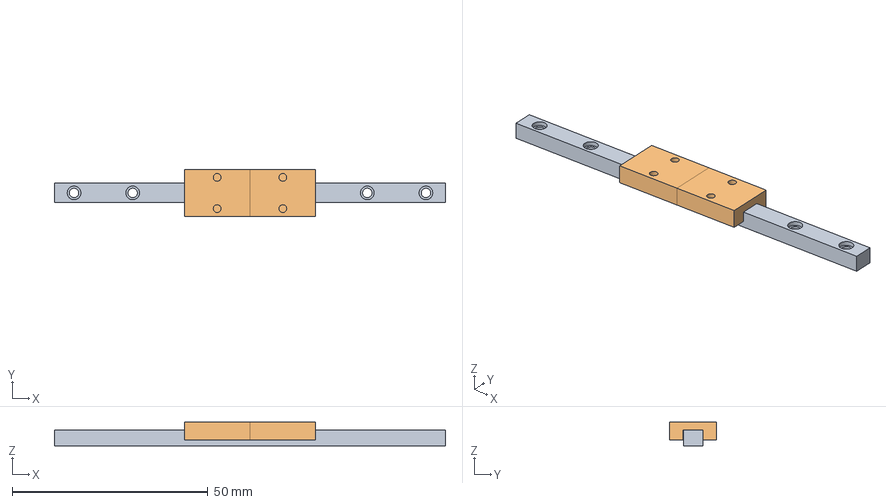
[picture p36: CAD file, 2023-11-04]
XL330_version/hardware/purchase_parts/stp/ref_SSE2B6-100.step
100.0 x 12.0 x 6.03 mm
ref_SSE2B6-100_rail_100mm
ref_SSE2B6-100_base x 2

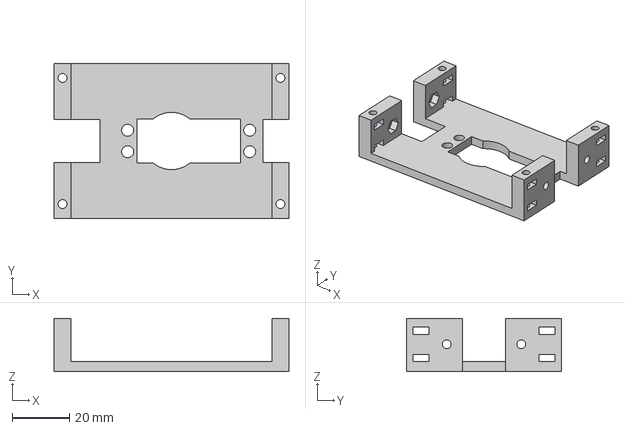
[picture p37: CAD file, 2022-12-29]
SCS3045M_version/hardware/3dprint_parts/SCS3045MBase.step
82.0 x 54.0 x 18.5 mm

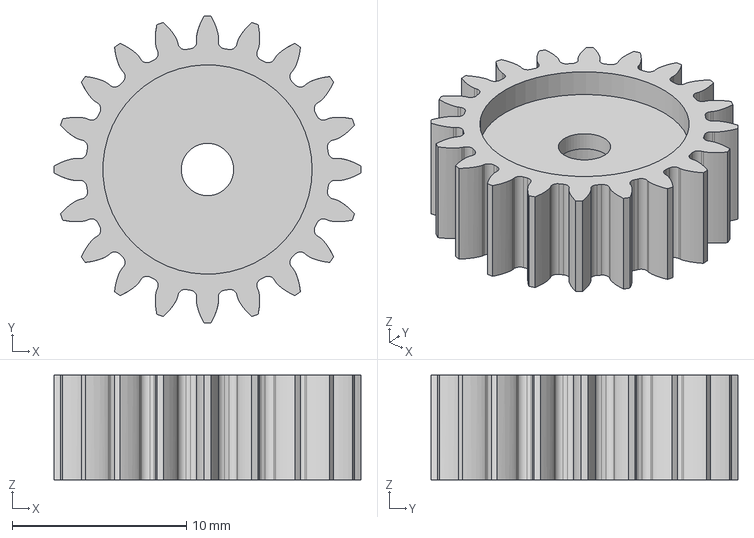
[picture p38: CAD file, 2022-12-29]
SCS3045M_version/hardware/purchase_parts/gear_20tooth.step
17.6 x 17.6 x 6.00 mm

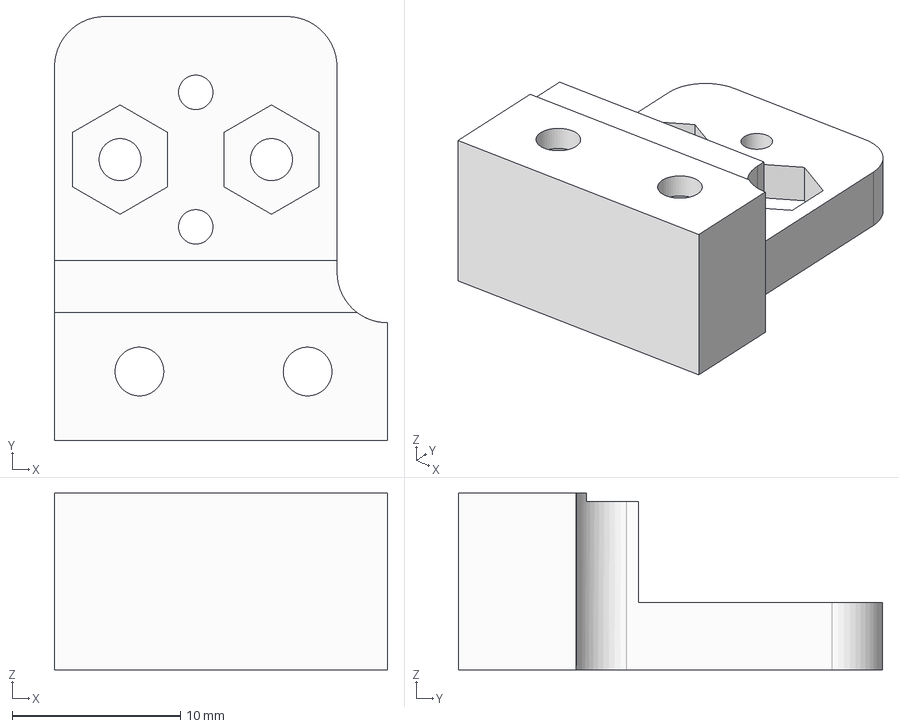
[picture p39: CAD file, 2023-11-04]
XL330_version/hardware/3dprint_parts/stp/rail_base_to_rack_dynamixel.step
19.8 x 25.2 x 10.5 mm

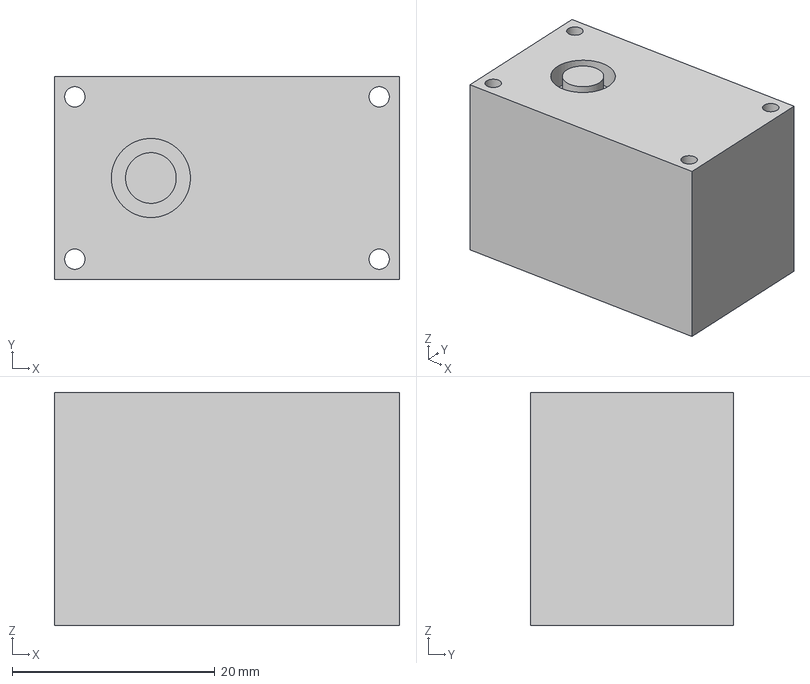
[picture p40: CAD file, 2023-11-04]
XL330_version/hardware/purchase_parts/stp/ref_XL330.step
34.0 x 20.0 x 23.0 mm

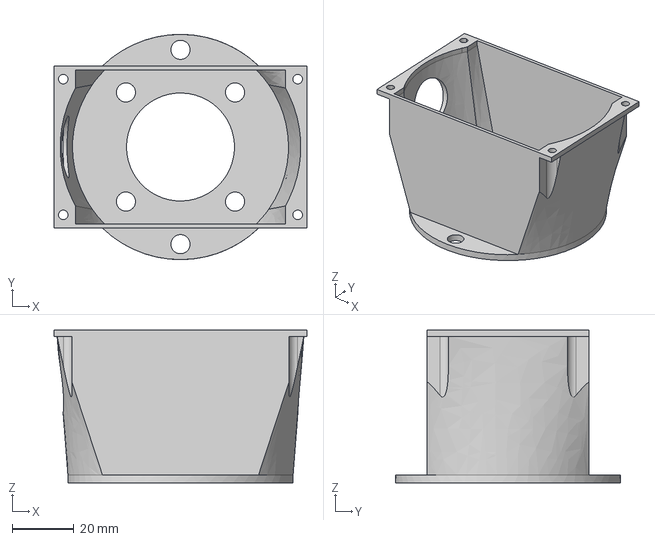
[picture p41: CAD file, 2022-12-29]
SCS3045M_version/hardware/3dprint_parts/ToArm.step
82.0 x 73.0 x 49.5 mm

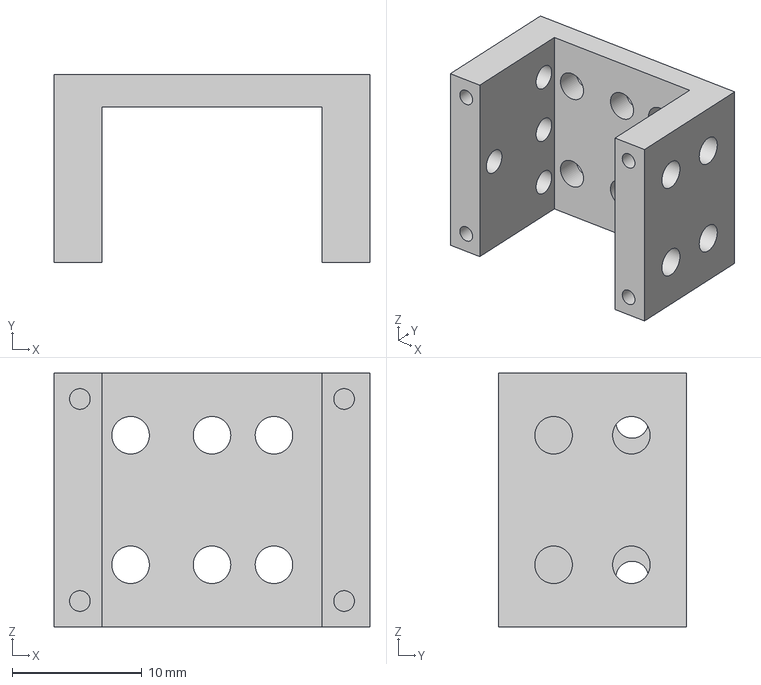
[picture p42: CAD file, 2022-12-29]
SCS3045M_version/hardware/cnc_miling_parts/rack_to_rail_base.step
24.4 x 14.5 x 19.6 mm

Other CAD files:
SCS3045M_version/hardware/cnc_miling_parts/claw50mm.step
SCS3045M_version/hardware/purchase_parts/SCS3045M.step
XL330_version/hardware/3dprint_parts/stp/XL330_cover.step
XL330_version/hardware/purchase_parts/stp/ref_RGEAL0.8KA-55-A5-B10-C10-D10.step
SCS3045M_version/hardware/3dprint_parts/stl/SCS3045MBase.stl
SCS3045M_version/hardware/3dprint_parts/stl/TipCover.stl
SCS3045M_version/hardware/3dprint_parts/stl/ToArm.stl
SCS3045M_version/hardware/cnc_miling_parts/claw_base.step
SCS3045M_version/hardware/cnc_miling_parts/rail_base_holder.step
SCS3045M_version/hardware/cnc_miling_parts/rail_fixer.step
SCS3045M_version/hardware/cnc_miling_parts/stl/claw50mm.stl
SCS3045M_version/hardware/cnc_miling_parts/stl/claw_base.stl
SCS3045M_version/hardware/cnc_miling_parts/stl/rack_to_rail_base.stl
SCS3045M_version/hardware/cnc_miling_parts/stl/rail_base_holder.stl
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

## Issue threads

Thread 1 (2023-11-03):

New design

hygradme, 2023-11-03:
The previous design(I call it SCS3045M_version):
[SCS3045M_version](https://github.com/hygradme/OpenParallelGripper/tree/XL330_version/SCS3045M_version)

which is basically ok if your target object is not heavy and if the object is hard material.
Still there are some issue:
- SCS3045M cannot use current control as kind of torque control and may have an issue when the gripper tries to grab a soft material(It may crush the object).
- It uses several CNC milling parts which raises the cost of the gripper manufacturing.
- The weight of the gripper is relatively light(about 340g) but still occupies over half of the payload of  UFACTORY Lite 6.

For these issue, I'm building a new gripper design using Dynamixel XL330-M288-T which can use current control.
The weight will be lighter by reducing the number of linear rails from two to one and in addition I changed the design to use more 3D printed parts which would be easy and cheap to make this gripper.

[XL330_version](https://github.com/hygradme/OpenParallelGripper/tree/XL330_version/XL330_version)

Which is not complete and need some more works.

Closed 2023-11-04.

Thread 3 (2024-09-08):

Control with MODBUS RTU throwing errors

Chompy80, 2024-09-08:
Hi,

I’m using the OpenRB-150 and XL330-M288-T as suggested in the XL330 version of your gripper.  the control with lite 6 python code works to open and close the gripper, but "control_openRB150_with_modbus_rtu" python script throws errors.  I have the robot's baud rate set to 115200, however I’m getting the following error:

$ python3 control_openRB150_with_modbus_rtu.py 10.10.0.182 coco
SDK_VERSION: 1.11.6
ROBOT_IP: 10.10.0.182, VERSION: v2.4.113, PROTOCOL: V1, DETAIL: 6,9,LI1006,DL1000,v2.4.113, TYPE1300: [0, 0]
change prot_flag to 3
[set_state], xArm is ready to move
set_tgpio_modbus_baudrate, code=0
[SDK][ERROR][2024-09-07 21:24:54][base.py:348] - - API -> getset_tgpio_modbus_data -> code=1, response=[]
[SDK][ERROR][2024-09-07 21:24:56][base.py:348] - - API -> getset_tgpio_modbus_data -> code=1, response=[]
[SDK][ERROR][2024-09-07 21:24:58][base.py:348] - - API -> getset_tgpio_modbus_data -> code=1, response=[]
[SDK][ERROR][2024-09-07 21:25:00][base.py:348] - - API -> getset_tgpio_modbus_data -> code=1, response=[]

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

hygradme, 2024-09-08:
Do you cross the TX and RX lines as described in the instruction?
https://github.com/hygradme/OpenParallelGripper/blob/XL330_version/XL330_version/electronics/grove_cross_cable.jpg
I also encountered same errors several times and usually it seems to be caused by wiring issues.

Chompy80, 2024-09-08:
Thank you for your reply.  I did swap the TX & RX wires as described.  I will go through all the instructions again to ensure everything else is wired properly.  For now, I’m able to control the gripper via analog signaling via the Lite 6.

Thank you so much for creating this repo.  I greatly appreciate you doing so, as I am now able to create grippers that don't rely on a vacuum pump!

hygradme, 2025-07-29:
@carltech22
What kind of data did you send from OpenRB-150?

hygradme, 2025-08-02:
I updated
[OpenRB_modbusRTU.ino](https://github.com/hygradme/OpenParallelGripper/blob/main/XL330_version/software/arduino_sketch/OpenRB_modbusRTU.ino) and [control_openRB150_with_modbus_rtu.py](https://github.com/hygradme/OpenParallelGripper/blob/main/XL330_version/software/examples/control_openRB150_with_modbus_rtu.py)
so that the host machine can receive the feedback of actual position of the gripper using Modbus-RTU.

Ideally, using Read Input Registers(0x04) function code looks suitable for this case to prevent the host machine from accidentally overwriting the gripper's actual position. However, xArm API(getset_tgpio_modbus_data) does not appear to support 0x04, so you have to use Read Holding Registers(0x03) instead to read data from the gripper.

https://github.com/hygradme/OpenParallelGripper/commit/659f8fa6a5ec498c10ee06df4e0bfafdb04946e6

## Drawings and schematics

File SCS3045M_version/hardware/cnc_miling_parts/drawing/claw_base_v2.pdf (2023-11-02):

18 ²⁷.6 | 14.6 4x Ø3.1 | 6x M3

2.49

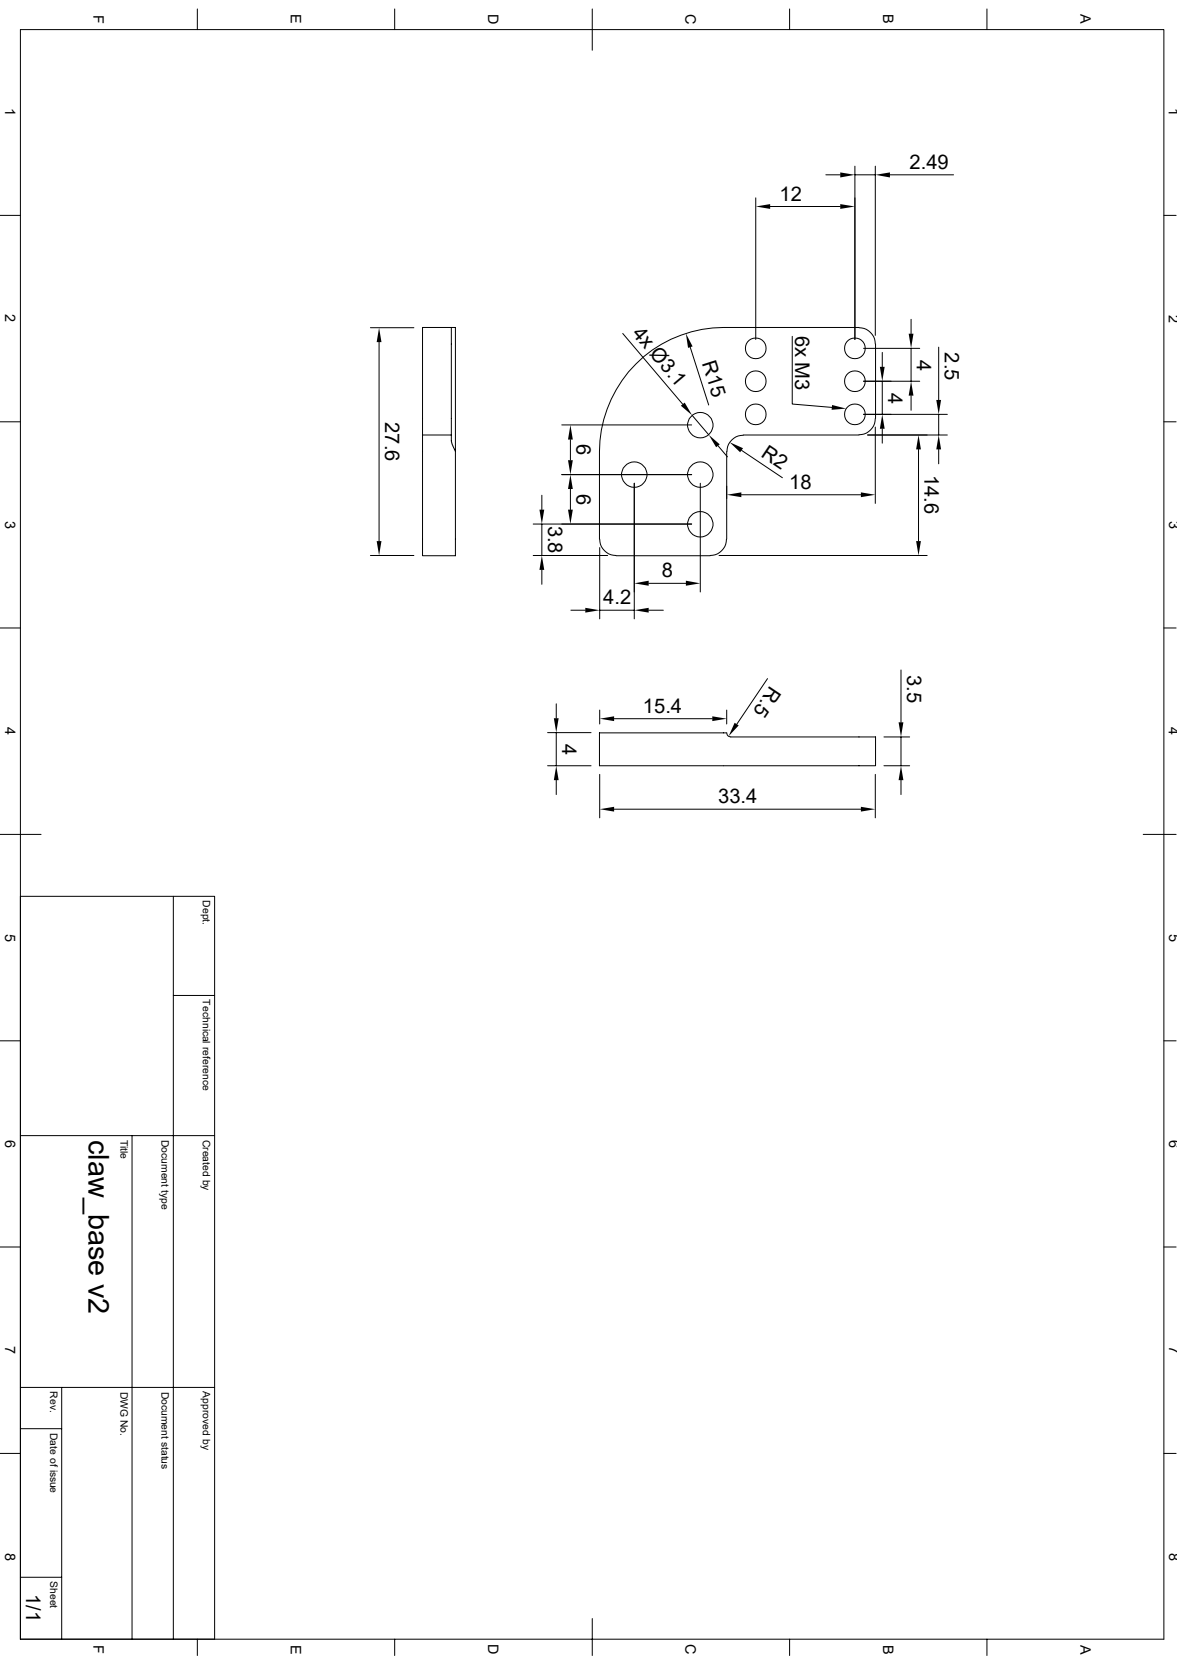
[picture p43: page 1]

1 A 2 3 4 5 6 7 8 1 2 3 4 5 6 7 8 FEDCB FEDCBA Dept. Technical reference Created by Approved by Title DWG No. Document type Document status Rev. Date of issue Sheet 1/1 claw_base v2 3.5

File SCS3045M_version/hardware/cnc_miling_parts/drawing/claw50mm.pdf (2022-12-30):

5.5

3.5 2x Ø3.1 | 5 | 3x Ø3.1 Ø5.5 2.5

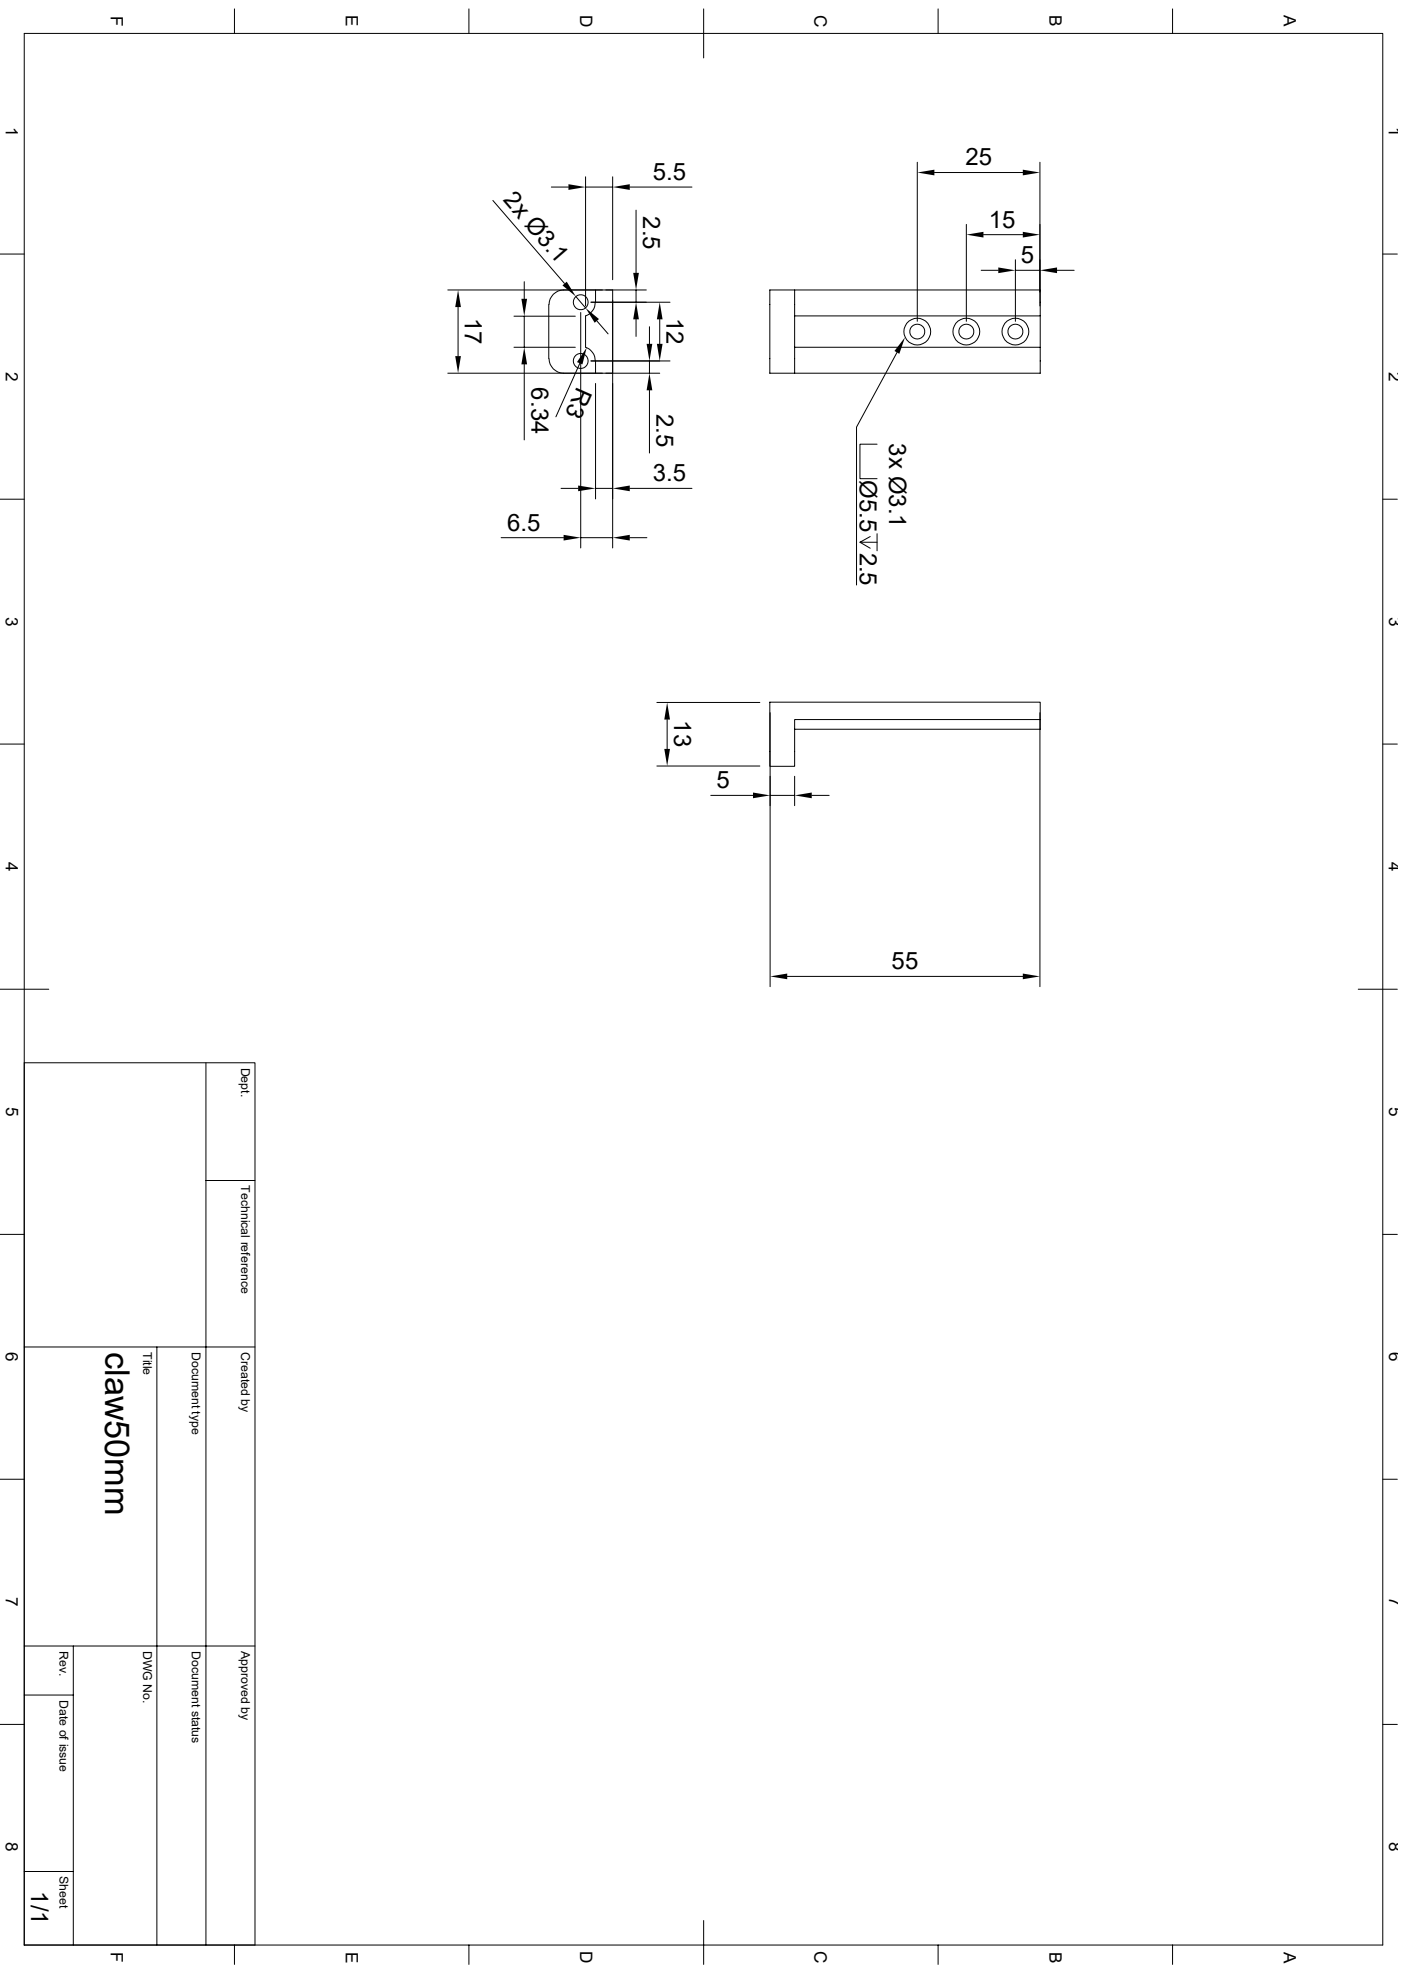
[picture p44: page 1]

1 A 2 3 4 5 6 7 8 1 2 3 4 5 6 7 8 FEDCB FEDCBA Dept. Technical reference Created by Approved by Title DWG No. Document type Document status Rev. Date of issue Sheet 1/1 claw50mm 17 13 6.34 R3

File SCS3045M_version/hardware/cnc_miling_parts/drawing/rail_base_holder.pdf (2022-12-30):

24.4 ¹⁹.6 | 5x M3 | 4x Ø2 Ø4 2 4x Ø2 R2 4 | 4 2 22 | 3.8 5.8 | 6 6 8

6.2 12

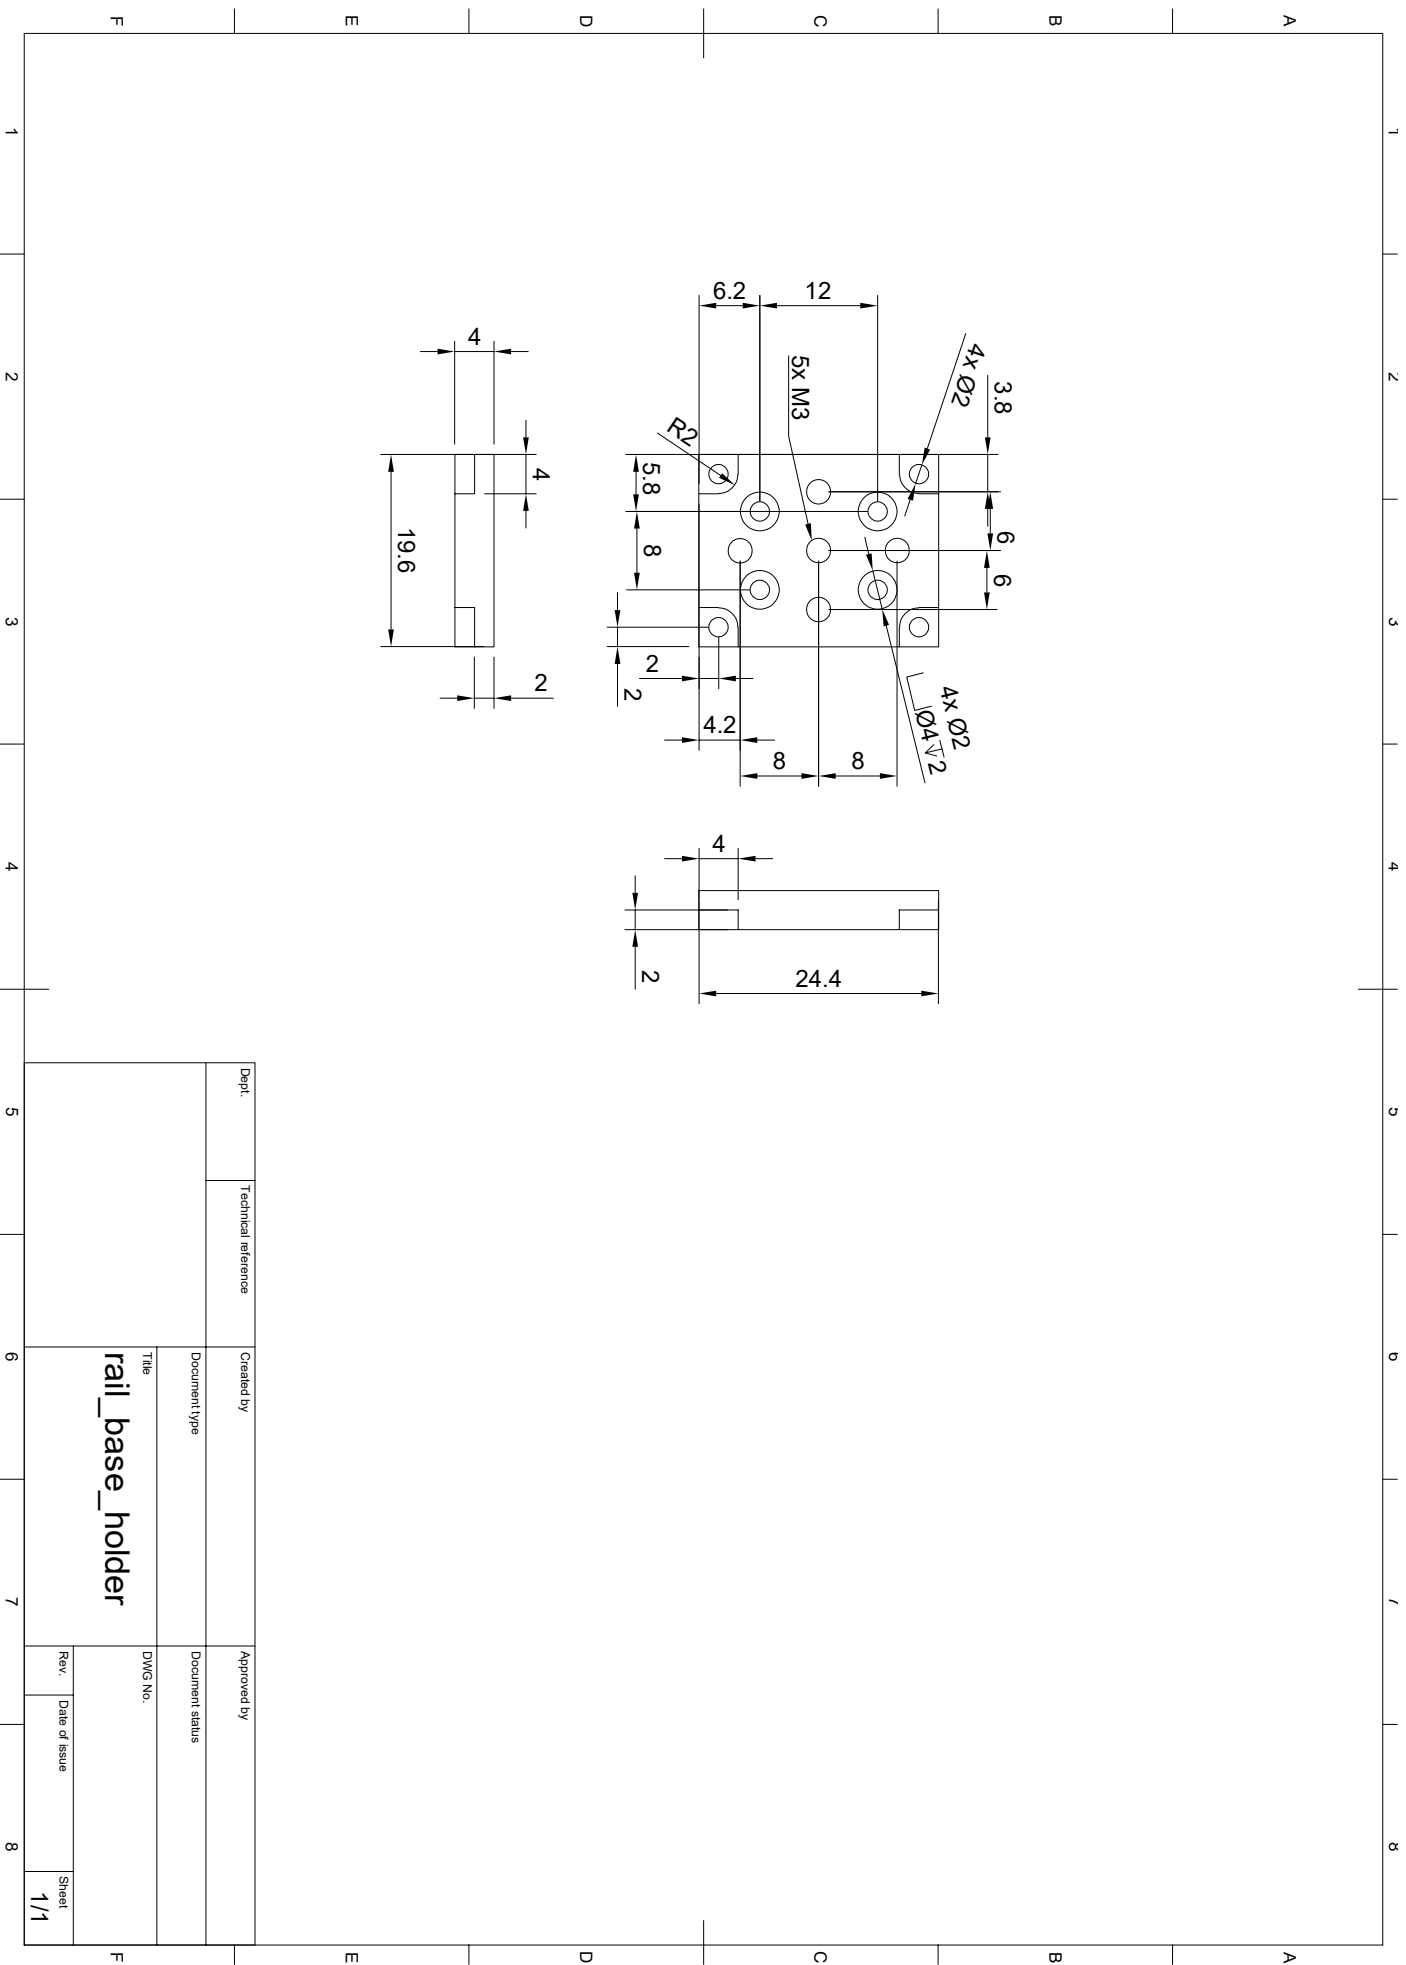
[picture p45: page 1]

1 A 2 3 4 5 6 7 8 1 2 3 4 5 6 7 8 FEDCB FEDCBA Dept. Technical reference Created by Approved by Title DWG No. Document type Document status Rev. Date of issue Sheet 1/1 rail_base_holder 4 2

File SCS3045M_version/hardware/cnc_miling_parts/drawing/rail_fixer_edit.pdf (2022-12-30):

12 | 12 ⁸ ⁶ | 3x Ø3.1 M2.3 M2.3 R3R3
22 | 22 | 4 ³ | 6 | 3

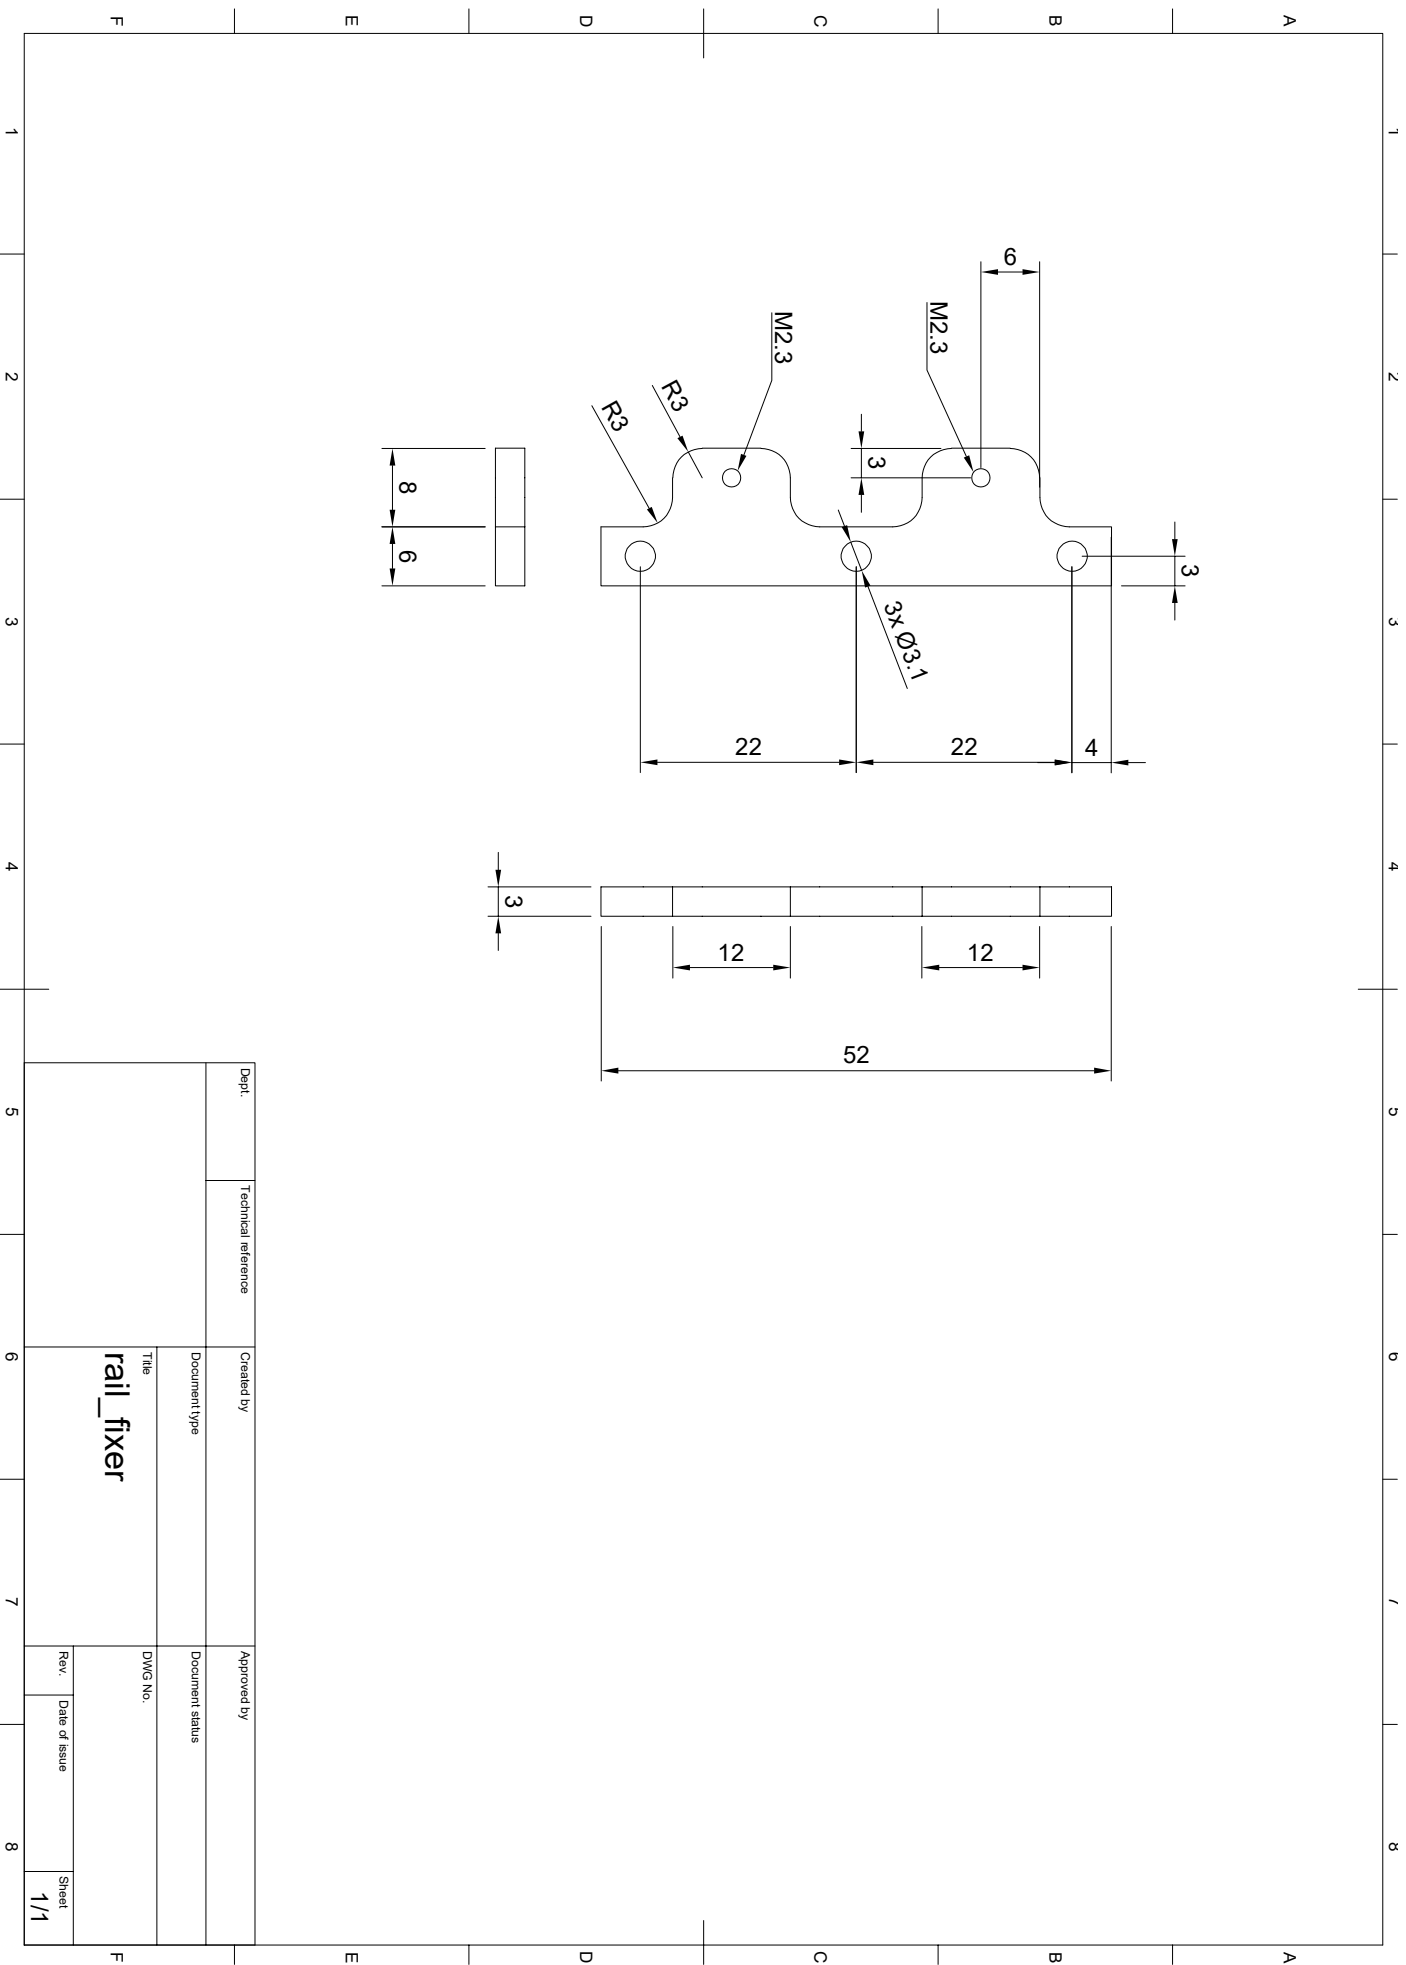
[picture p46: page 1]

1 A 2 3 4 5 6 7 8 1 2 3 4 5 6 7 8 FEDCB FEDCBA Dept. Technical reference Created by Approved by Title DWG No. Document type Document status Rev. Date of issue Sheet 1/1 rail_fixer

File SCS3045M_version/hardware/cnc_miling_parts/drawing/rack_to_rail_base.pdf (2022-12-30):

17 | 14.512 4x M3.5 | M3 M3 M3 4x M2 | M3 3 6x M3.5 19.6 | 8 | 2.31 ³.78 6 6
4.25 6 | 4.8 10 | 4.8

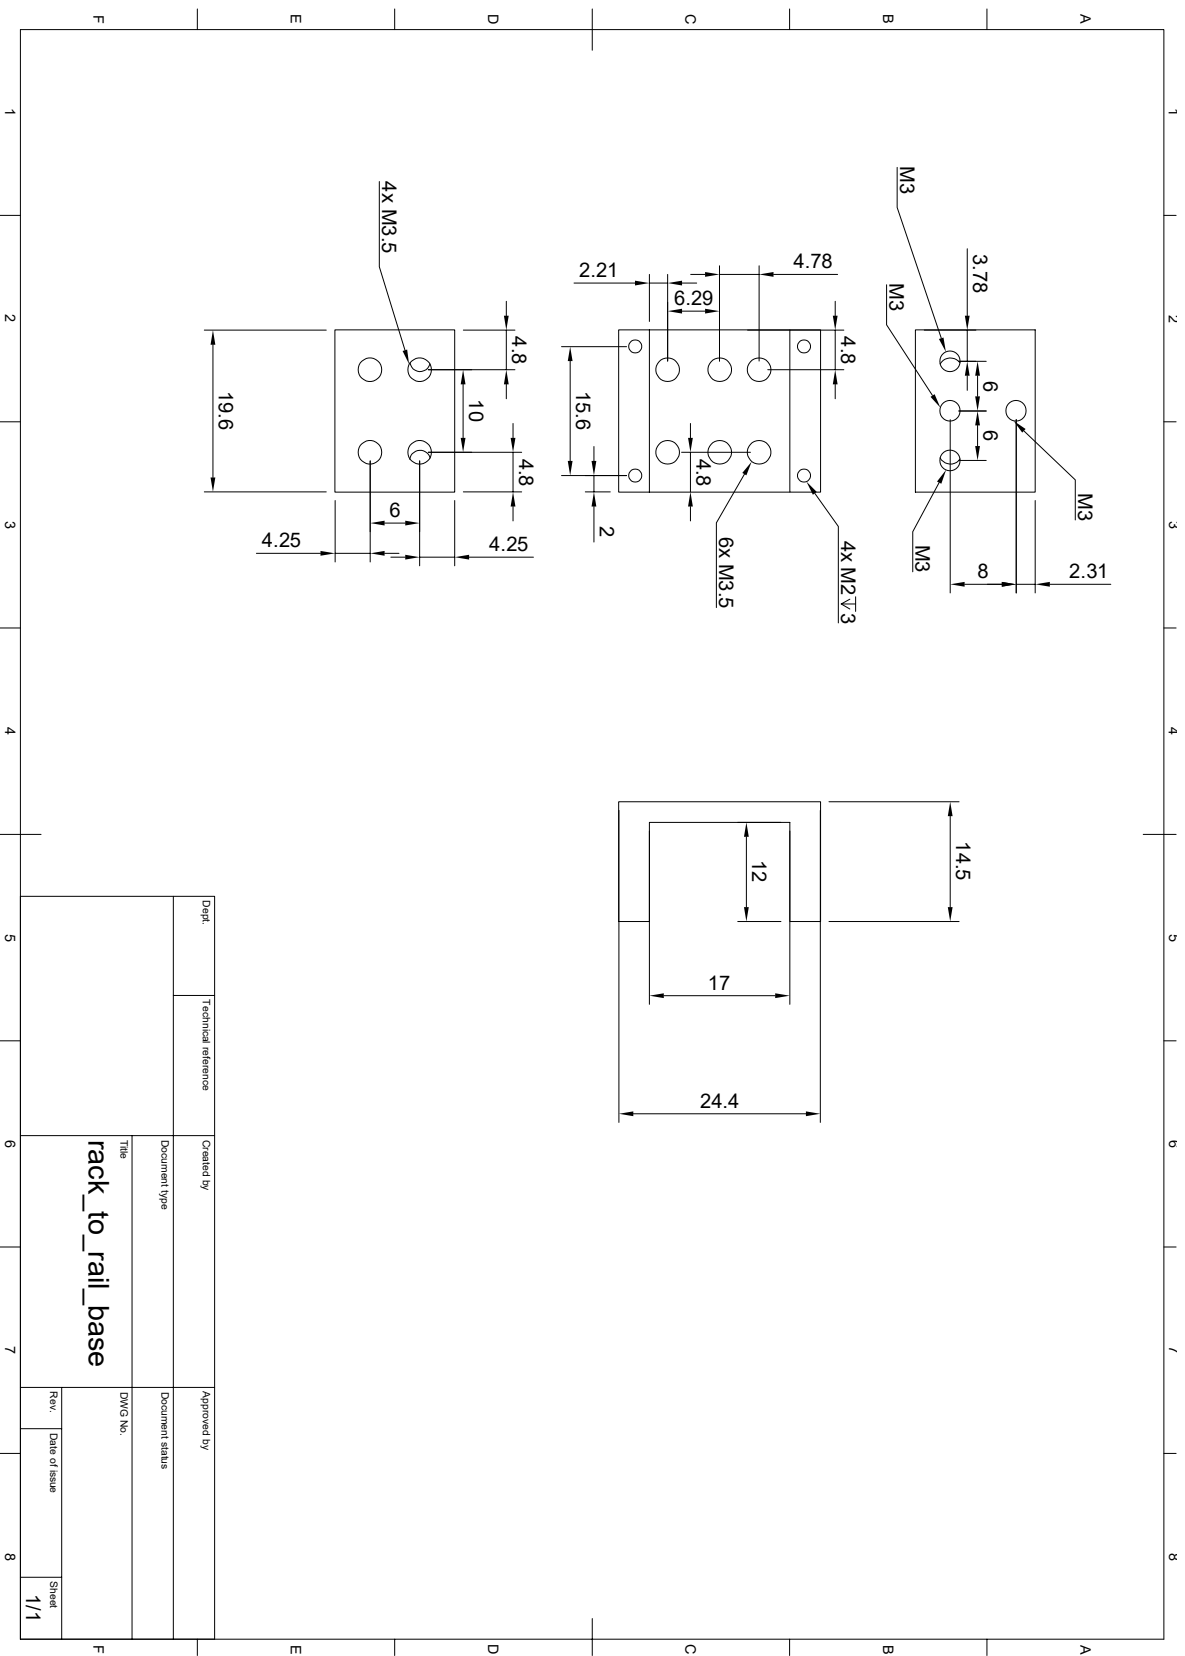
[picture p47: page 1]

1 A 2 3 4 5 6 7 8 1 2 3 4 5 6 7 8 FEDCB FEDCBA Dept. Technical reference Created by Approved by Title DWG No. Document type Document status Rev. Date of issue Sheet 1/1 rack_to_rail_base

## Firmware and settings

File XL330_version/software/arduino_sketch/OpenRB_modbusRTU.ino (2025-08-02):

#include <Dynamixel2Arduino.h>
#include <ModbusRTU.h>

#define DXL_SERIAL Serial1
#define DEBUG_SERIAL Serial
const int DXL_DIR_PIN = -1;

ModbusRTU mb;
#define SLAVE_ID 1

#define REG_GRIPPER_POS 128
#define REG_READ_GRIPPER_POS 257

#define LITE6_OUTPUT0 4
#define LITE6_OUTPUT1 5

int lite6_0;
int lite6_1;
uint16_t gripper_pos = 0;
uint16_t gripper_open_pos = 250;// 150 for 75mm rail version
uint16_t gripper_close_pos = 0;

const uint8_t DXL_ID = 1;
const float DXL_PROTOCOL_VERSION = 2.0;
int current_val = 75;//50;

const int32_t PROFILE_VELOCITY_VALUE = 300;  // vel（unit: 0.229 rpm, 300 = 68.7rpm）
const int32_t PROFILE_ACCELERATION_VALUE = 50; // acc（unit: 214.577rev/min^2）

Dynamixel2Arduino dxl(DXL_SERIAL, DXL_DIR_PIN);

using namespace ControlTableItem;

void setup() {
  pinMode(LITE6_OUTPUT0, INPUT_PULLUP);
  pinMode(LITE6_OUTPUT1, INPUT_PULLUP);

  dxl.begin(57600);
  dxl.setPortProtocolVersion(DXL_PROTOCOL_VERSION);
  dxl.ping(DXL_ID);

  dxl.torqueOff(DXL_ID);
  dxl.setOperatingMode(DXL_ID, OP_CURRENT_BASED_POSITION);

  dxl.writeControlTableItem(PROFILE_VELOCITY, DXL_ID, PROFILE_VELOCITY_VALUE);
  dxl.writeControlTableItem(PROFILE_ACCELERATION, DXL_ID, PROFILE_ACCELERATION_VALUE);

  dxl.torqueOn(DXL_ID);

  DEBUG_SERIAL.begin(115200);
  
  // modbus RTU
  // Serial2.begin(115200, SERIAL_8N1);
  Serial2.begin(57600, SERIAL_8N1);
  mb.begin(&Serial2);
  mb.slave(SLAVE_ID);

  mb.addHreg(REG_GRIPPER_POS);
  mb.Hreg(REG_GRIPPER_POS, gripper_pos);
  mb.addHreg(REG_READ_GRIPPER_POS, 0);
  delay(1000);
}

void loop() {
    lite6_0 = digitalRead(LITE6_OUTPUT0);
    lite6_1 = digitalRead(LITE6_OUTPUT1);
    if(lite6_0 == LOW && lite6_1 == HIGH){
      dxl.setGoalCurrent(DXL_ID, current_val);
      dxl.setGoalPosition(DXL_ID, gripper_open_pos, UNIT_DEGREE);
    }
    else if(lite6_0 == HIGH && lite6_1 == LOW){
      dxl.setGoalCurrent(DXL_ID, current_val);
      dxl.setGoalPosition(DXL_ID, gripper_close_pos, UNIT_DEGREE);
    }
    else if(lite6_0 == LOW && lite6_1 == LOW){

      gripper_pos = mb.Hreg(REG_GRIPPER_POS);
      dxl.setGoalCurrent(DXL_ID, current_val);
      dxl.setGoalPosition(DXL_ID, gripper_pos, UNIT_DEGREE);
      DEBUG_SERIAL.print("Present gripper_pos(target) : ");
      DEBUG_SERIAL.println(gripper_pos);
    }

    // write current position to holding register
    float present_deg = dxl.getPresentPosition(DXL_ID, UNIT_DEGREE);
    mb.Hreg(REG_READ_GRIPPER_POS, (uint16_t)present_deg);

    mb.task();
    yield();

}

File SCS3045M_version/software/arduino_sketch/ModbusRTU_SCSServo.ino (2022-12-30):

#include <SCServo.h>
#include "M5Atom.h"
#include <ModbusRTU.h>

SMS_STS sms_sts;
unsigned int SERVO_POS = 0;

#define TX_UART 33
#define RX_UART 23
 
// modbus-rtu setup
#define RX_MODBUS 32
#define TX_MODBUS 26
#define SLAVE_ID 1
#define REGN 10
#define REG_GRIPPER_POS 128
#define REG_READ_GRIPPER_POS 257

#define LITE6_OUTPUT0 21
#define LITE6_OUTPUT1 22

int lite6_0;
int lite6_1;
uint16_t gripper_pos = 1500;
uint16_t gripper_open_pos = 2200;
uint16_t gripper_close_pos = 200;

ModbusRTU mb;

void setup() {

  pinMode(LITE6_OUTPUT0, INPUT_PULLUP);
  pinMode(LITE6_OUTPUT1, INPUT_PULLUP);
  // put your setup code here, to run once:
  M5.begin(true, false, true);

  // for servo control uart
  Serial1.begin(1000000, SERIAL_8N1, RX_UART, TX_UART);
  sms_sts.pSerial = &Serial1;

  // modbus rtu
  Serial2.begin(115200, SERIAL_8N1, RX_MODBUS, TX_MODBUS);
  mb.begin(&Serial2);
  mb.slave(SLAVE_ID);

  mb.addHreg(REG_GRIPPER_POS);
  mb.Hreg(REG_GRIPPER_POS,  gripper_pos);
  mb.addIreg(REG_READ_GRIPPER_POS, gripper_pos);

  delay(1000);
}

void loop() {
  // with digital input
  lite6_0 = digitalRead(LITE6_OUTPUT0);
  lite6_1 = digitalRead(LITE6_OUTPUT1);
  if(lite6_0 == LOW && lite6_1 == HIGH){
    sms_sts.WritePosEx(1, gripper_open_pos, 2500, 200);    
   }
  if(lite6_0 == HIGH && lite6_1 == LOW){
    sms_sts.WritePosEx(1, gripper_close_pos, 2500, 200);    
   }

  // with modbus control mode
  if(lite6_0 == HIGH && lite6_1 == HIGH){

    gripper_pos = mb.Hreg(REG_GRIPPER_POS);
    
    sms_sts.WritePosEx(1, gripper_pos, 2500, 200);  
  }

  mb.task();
  yield();
}

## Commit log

2022-12-29 add hardware
    [RSEB8-70_base.step, RSEB8-70_rail.step, Rack_RGEAL0.8KA-40.step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]
2022-12-30 add electronics, software. update readme, bom
2022-12-30 change case
2022-12-30 add arduino sketch for ATOM Lite
2023-01-07 Fix height of TipConver to avoid interference with bolt head. Add assemble video instruction link to README.md
    [TipCover.step, TipCover.stl, gripper_assembly.step]
2023-11-02 minor update. Little lighter claw_base as v2
    [claw_base_v2.step]
2023-11-02 add XL330_version
    [Claw_50mm.step, Claw_50mm.stl, Gear20Tooth_forXL330.step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]
2023-11-04 Add README.md of XL330_version. Update BOM.md
2025-08-02 update get_pos of modbus-rtu example and .ino using Holding register(0x03) to get current position feedback from a gripper
